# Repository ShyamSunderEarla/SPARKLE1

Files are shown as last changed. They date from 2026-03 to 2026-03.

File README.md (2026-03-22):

This is a multifunctional flight computer which uses an STM32F722 microcontroller for data processing and commands. The sensors used in this are LSM6dS3 as the IMU and MS5611 as the barometer for the altitude measuremet. This has an onboard 5v and 3.3v buck converters. There is an onboard flash for data logging along with an SD card slot.

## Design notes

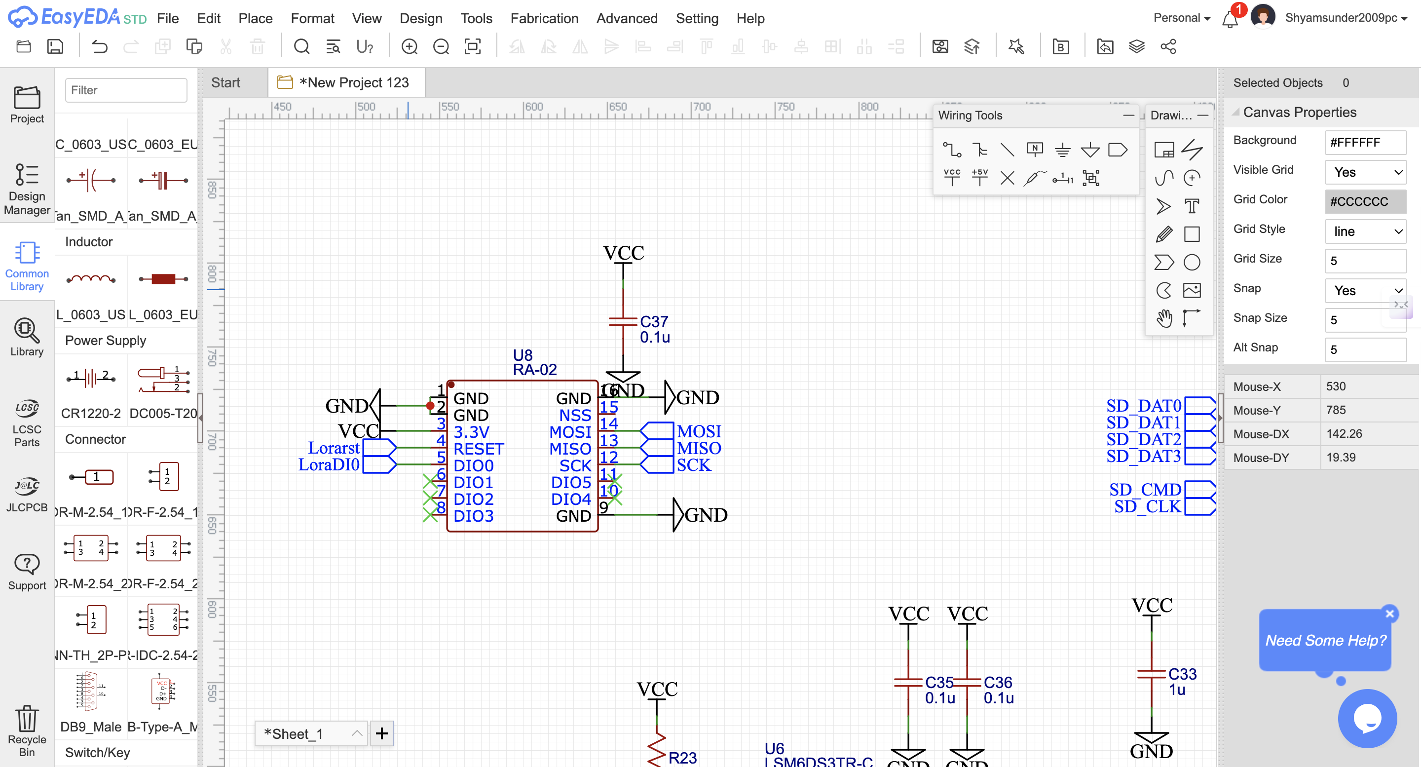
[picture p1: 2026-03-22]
assets/Screenshot 2026-03-17 at 1.37.54 PM.png

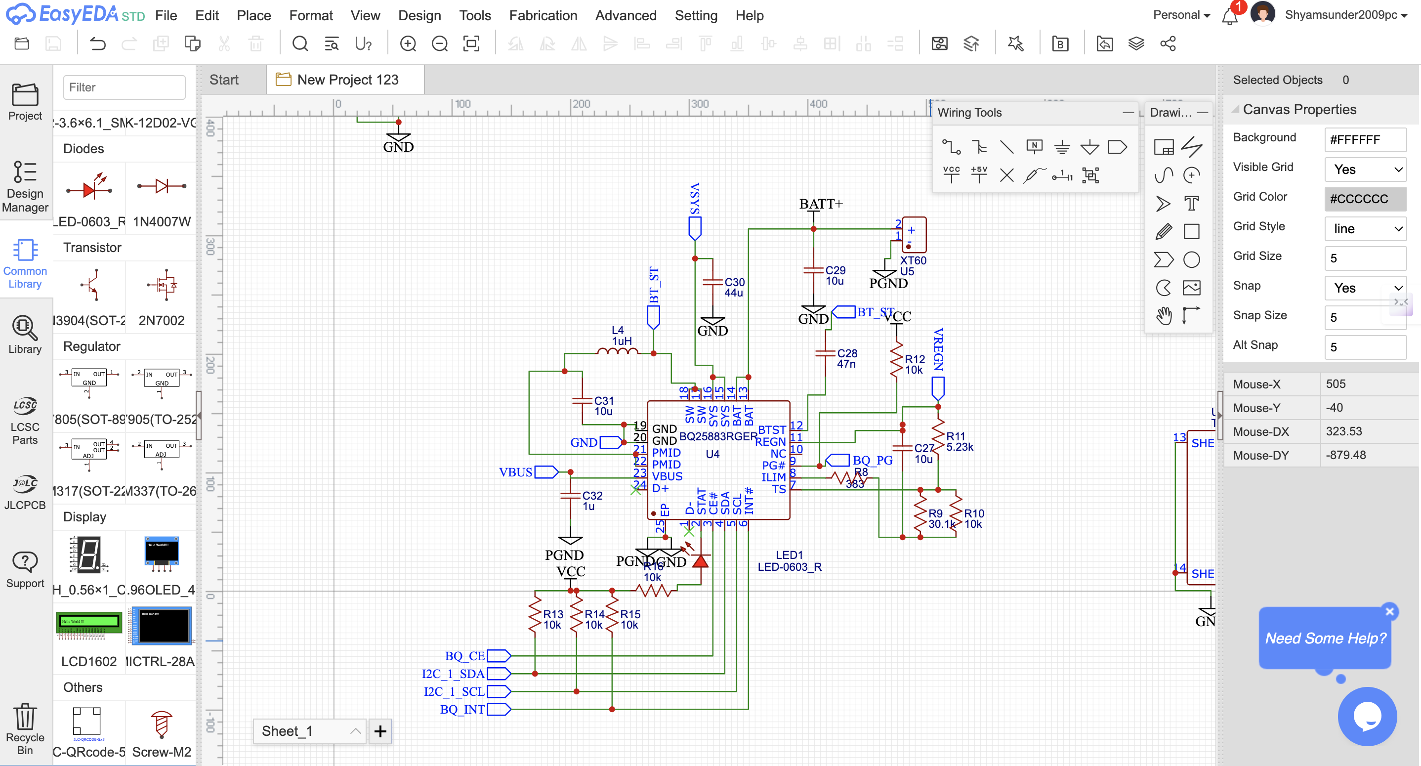
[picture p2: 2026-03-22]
assets/Screenshot 2026-03-16 at 3.34.25 PM.png

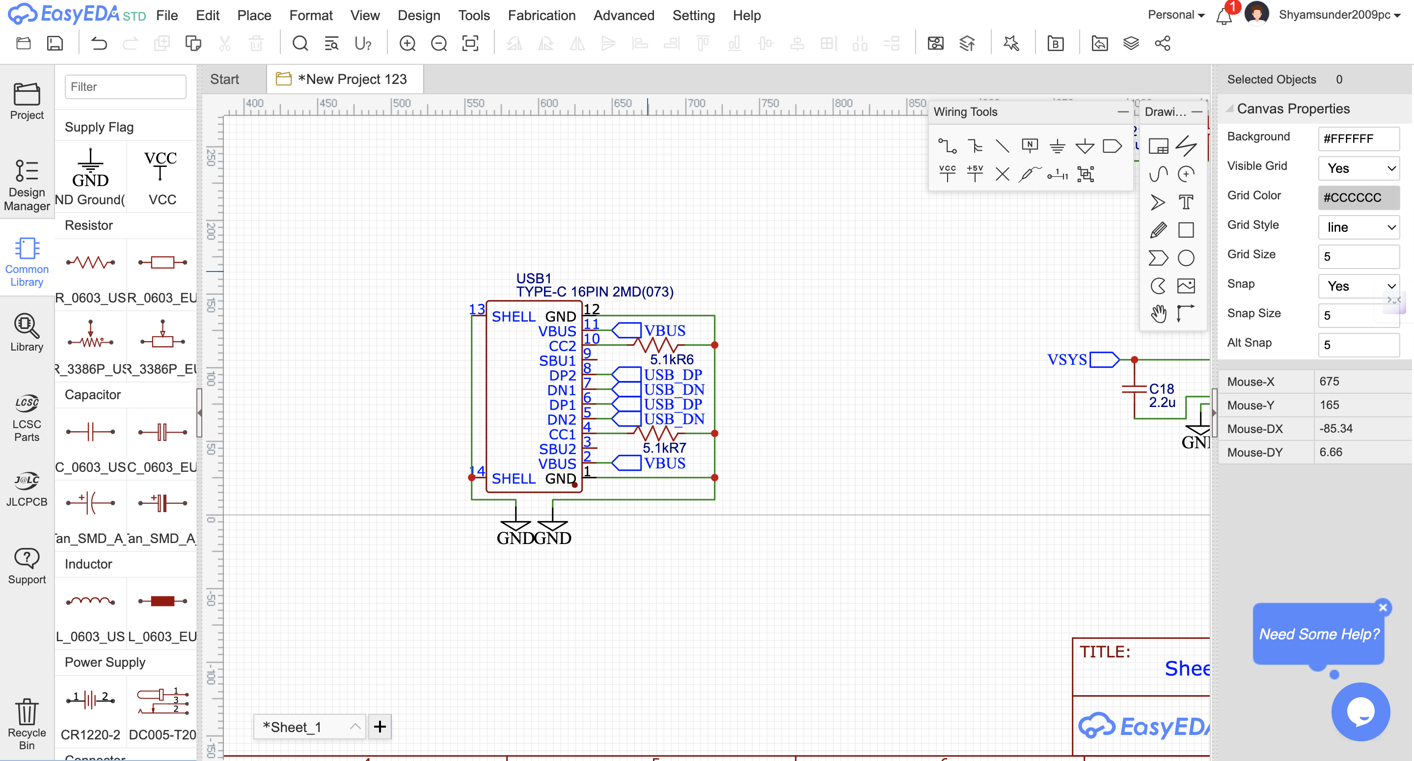
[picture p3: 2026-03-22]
assets/Screenshot 2026-03-16 at 2.43.29 PM.png

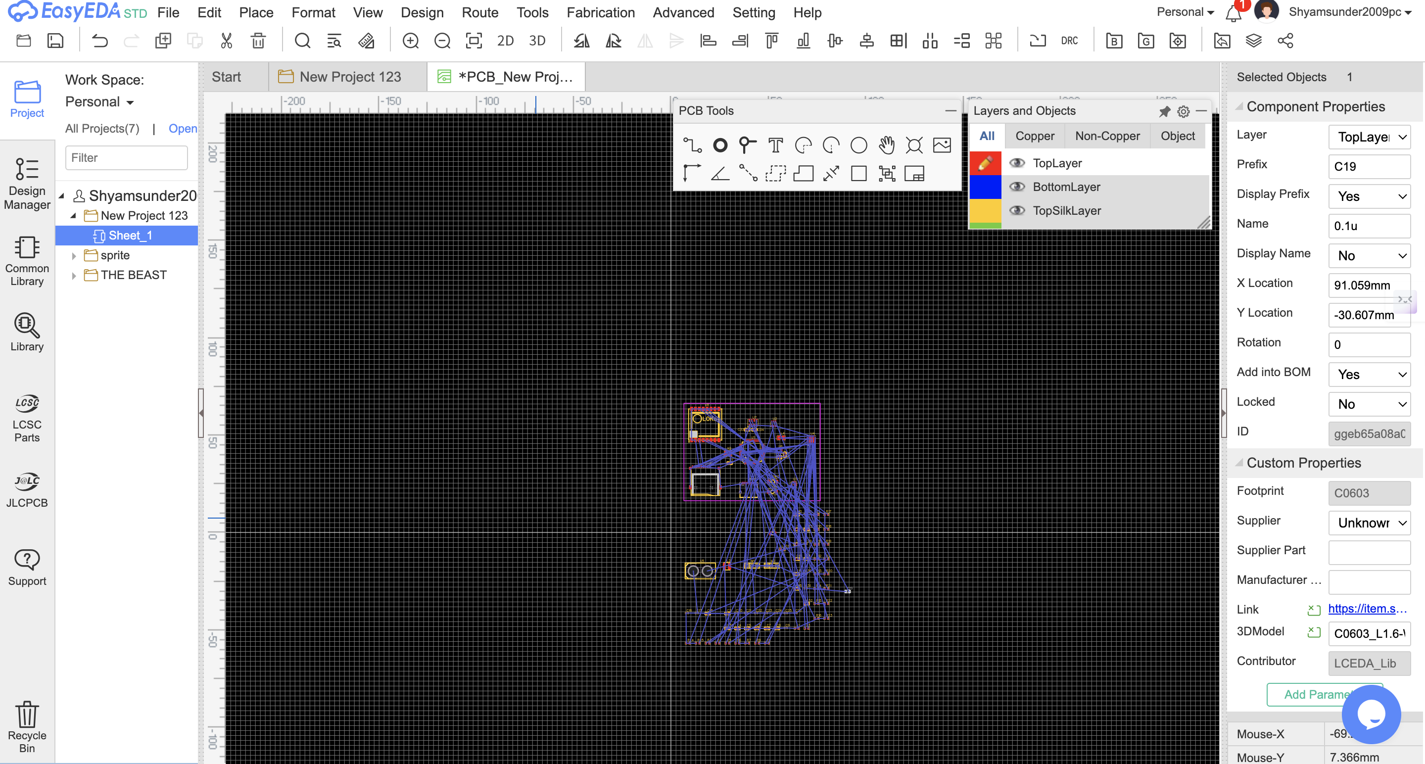
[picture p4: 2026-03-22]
assets/Screenshot 2026-03-18 at 9.15.15 AM.png

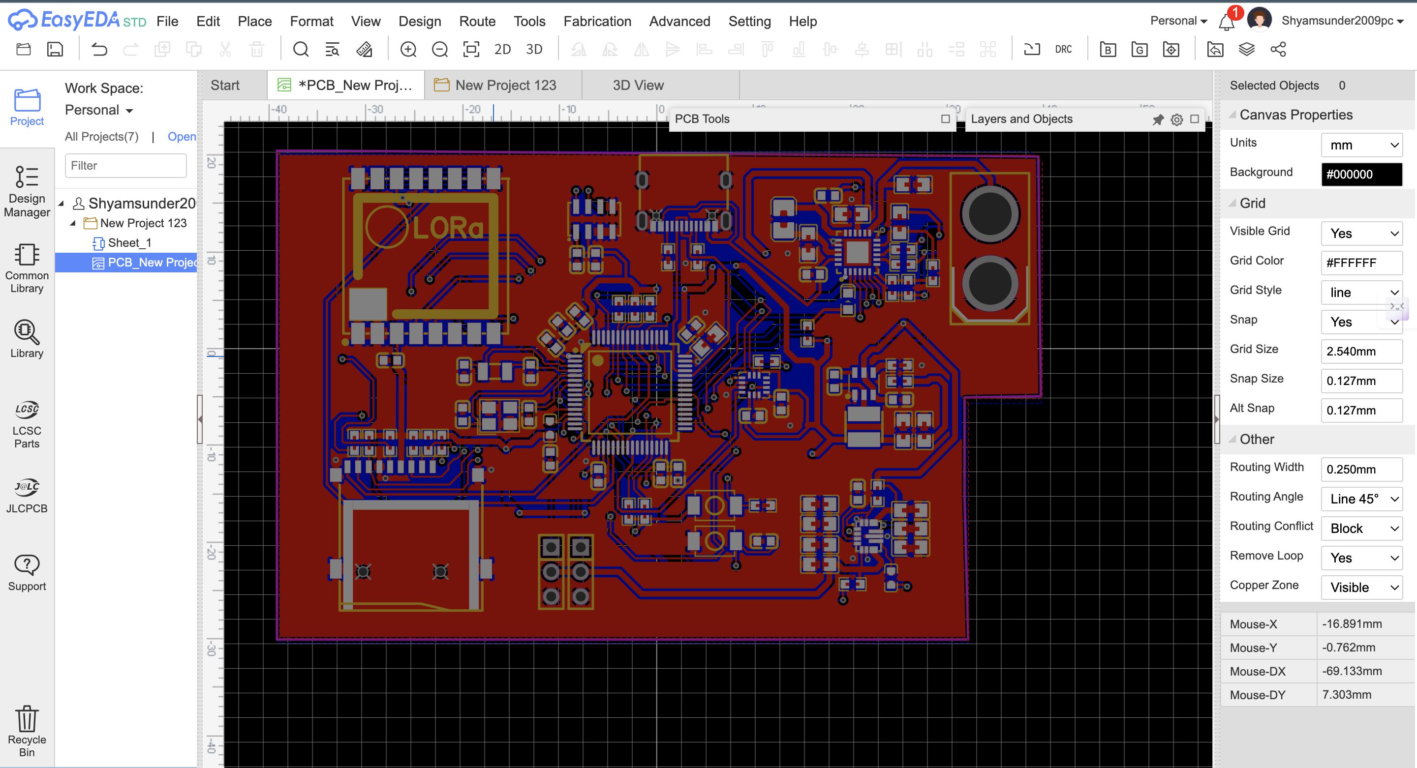
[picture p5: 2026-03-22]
assets/Screenshot 2026-03-22 at 12.50.01 PM.png

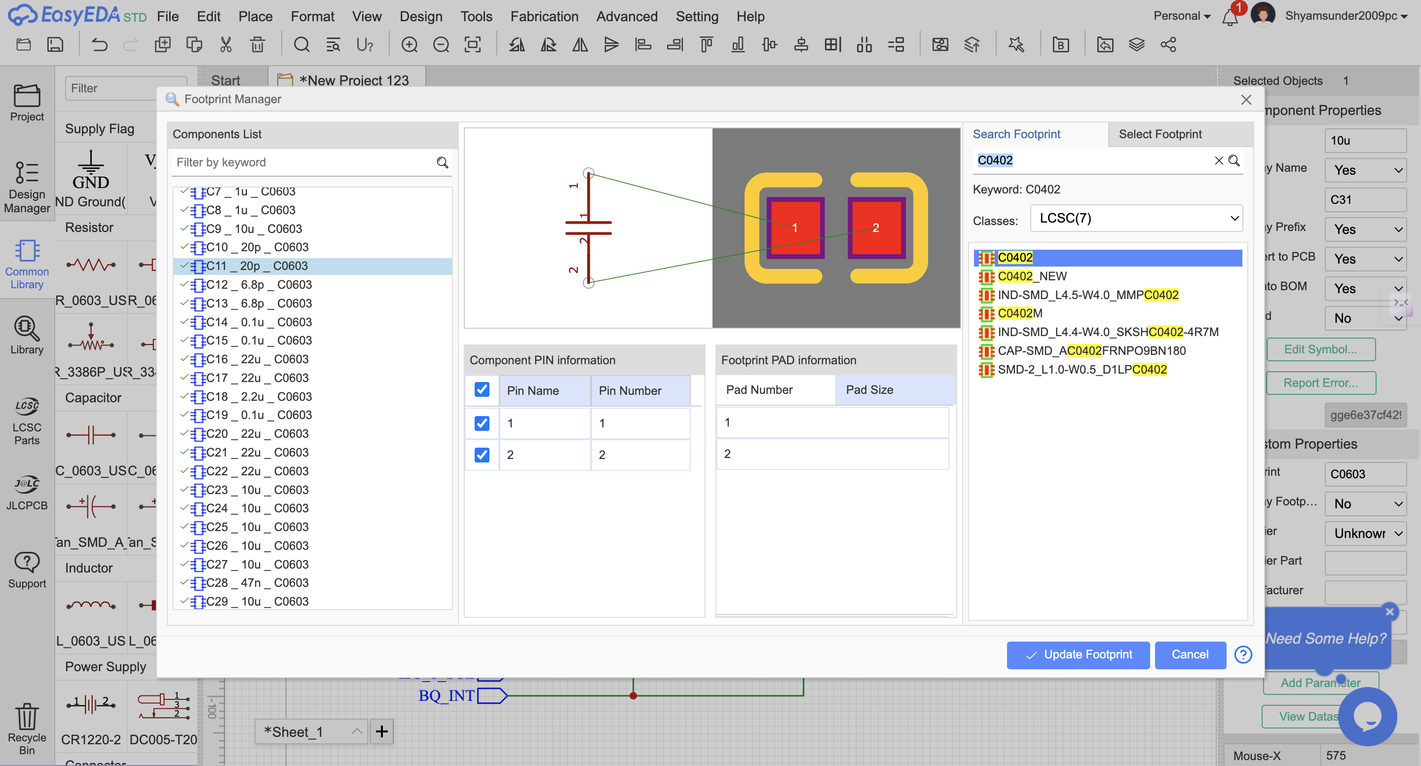
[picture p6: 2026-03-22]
assets/Screenshot 2026-03-17 at 1.45.49 PM.png

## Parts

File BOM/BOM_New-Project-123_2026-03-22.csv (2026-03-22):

ID | Name | Designator | Footprint | Quantity | Manufacturer Part | Manufacturer | Supplier | Supplier Part | Price
1 | 0.1u | C1,C2,C3,C4,C5,C14,C15,C19,C34,C35,C36,C37 | C0603 | 12
2 | 1u | C6,C7,C8,C32,C33 | C0603 | 5
3 | 20p | C10,C11 | C0603 | 2
4 | 6.8p | C12,C13 | C0603 | 2
5 | 2.2u | C18 | C0603 | 1
6 | 47n | C28 | C0603 | 1
7 | TF-01A | CARD1 | TF-SMD_TF-01A | 1 | TF-01A | 韩国韩荣 | LCSC | C91145 | 0.188
8 | FCM1608KF-601T03 | L1 | L0603 | 1 | FCM1608KF-601T03 | TAI-TECH(台庆) | LCSC | C141723 | 0.008
9 | 5.6uH | L2 | IND-SMD_L3.0-W3.0 | 1 | YHNR3015-5R6M | YJYCOIN(益嘉源) | LCSC | C18236327 | 0.009
10 | 1u | L3 | L0603 | 1
11 | 1uH | L4 | L2520 | 1 | DFE252012F-1R0M=P2 | muRata(村田) | LCSC | C435392 | 0.14
12 | LED-0603_R | LED1 | LED0603_RED | 1 | 19-217/R6C-AL1M2VY/3T | EVERLIGHT(台湾亿光) | LCSC | C72044 | 0.021
13 | Motor_Servo | M1,M2 | HDR-TH_PZ254V-11-03P-YL | 2
14 | 10k | R1,R4,R5,R10,R12,R13,R14,R15,R16,R17,R18,R19,R20,R21,R22,R23 | R0603 | 16
15 | 100k | R2 | R0603 | 1
16 | 22.1k | R3 | R0603 | 1
17 | 5.1k | R6,R7 | R0603 | 2
18 | 383 | R8 | R0603 | 1
19 | 30.1k | R9 | R0603 | 1
20 | 5.23k | R11 | R0603 | 1
21 | 2k2 | R24,R25 | R0603 | 2
22 | TS-1088-AR02016 | SW1,SW2 | SW-SMD_L3.9-W3.0-P4.45 | 2 | TS-1088-AR02016 | XUNPU(讯普) | LCSC | C720477 | 0.054
23 | STM32F722RET6 | U1 | LQFP-64_L10.0-W10.0-P0.50-LS12.0-BL | 1 | STM32F722RET6 | ST(意法半导体) | LCSC | C118207 | 6.353
24 | LMR51430XDDCR | U2 | SOT-23-6_L2.9-W1.6-P0.95-LS2.8-BL | 1 | LMR51430XDDCR | TI(德州仪器) | LCSC | C5185863 | 0.913
25 | BQ25883RGER | U4 | VFQFPN-24_L4.0-W4.0-P0.50-BL-EP2.8 | 1 | BQ25883RGER | TI(德州仪器) | LCSC | C544362 | 2.977
26 | XT60 | U5 | CONN-TH_XT60 | 1 | XT60-M. | AMASS(艾迈斯) | LCSC | C98733 | 0.322
27 | LSM6DS3TR-C | U6 | LGA-14_L3.0-W2.5-P0.50-TL | 1 | LSM6DS3TR-C | ST(意法半导体) | LCSC | C967633 | 2.789
28 | MS561101BA03-50 | U7 | SENSORS-SMD_MS5611-01BA03 | 1 | MS561101BA03-50 | TE Connectivity(泰科电子) | LCSC | C15639 | 6.615
29 | RA-02 | U8 | WIRELM-SMD_RA-02-BL | 1 | Ra-02 | Ai-Thinker(安信可) | LCSC | C90039 | 7.011
30 | TYPE-C 16PIN 2MD(073) | USB1 | USB-C-SMD_TYPE-C-6PIN-2MD-073 | 1 | TYPE-C 16PIN 2MD(073) | SHOU HAN(首韩) | LCSC | C2765186 | 0.065
31 | 32.768kHz | X1 | FC-135R_L3.2-W1.5 | 1 | Q13FC13500004 | EPSON(爱普生) | LCSC | C32346 | 0.176
32 | 25MHz | X2 | CRYSTAL-SMD_4P-L3.2-W2.5-BL | 1 | X322525MOB4SI | YXC(扬兴晶振) | LCSC | C9006 | 0.073
33 | 10u | C9,C23,C24,C25,C26,C27,C29,C31 | C0805 | 8
34 | 22u | C16,C17,C20,C21,C22 | C0805 | 5
35 | 44u | C30 | C0805 | 1
36 | TPS63070RNMR | U3 | VQFN-15-HR(3X2.5) | 1 | TPS63070RNMR | TI(德州仪器) | LCSC | C109322 | 1.38

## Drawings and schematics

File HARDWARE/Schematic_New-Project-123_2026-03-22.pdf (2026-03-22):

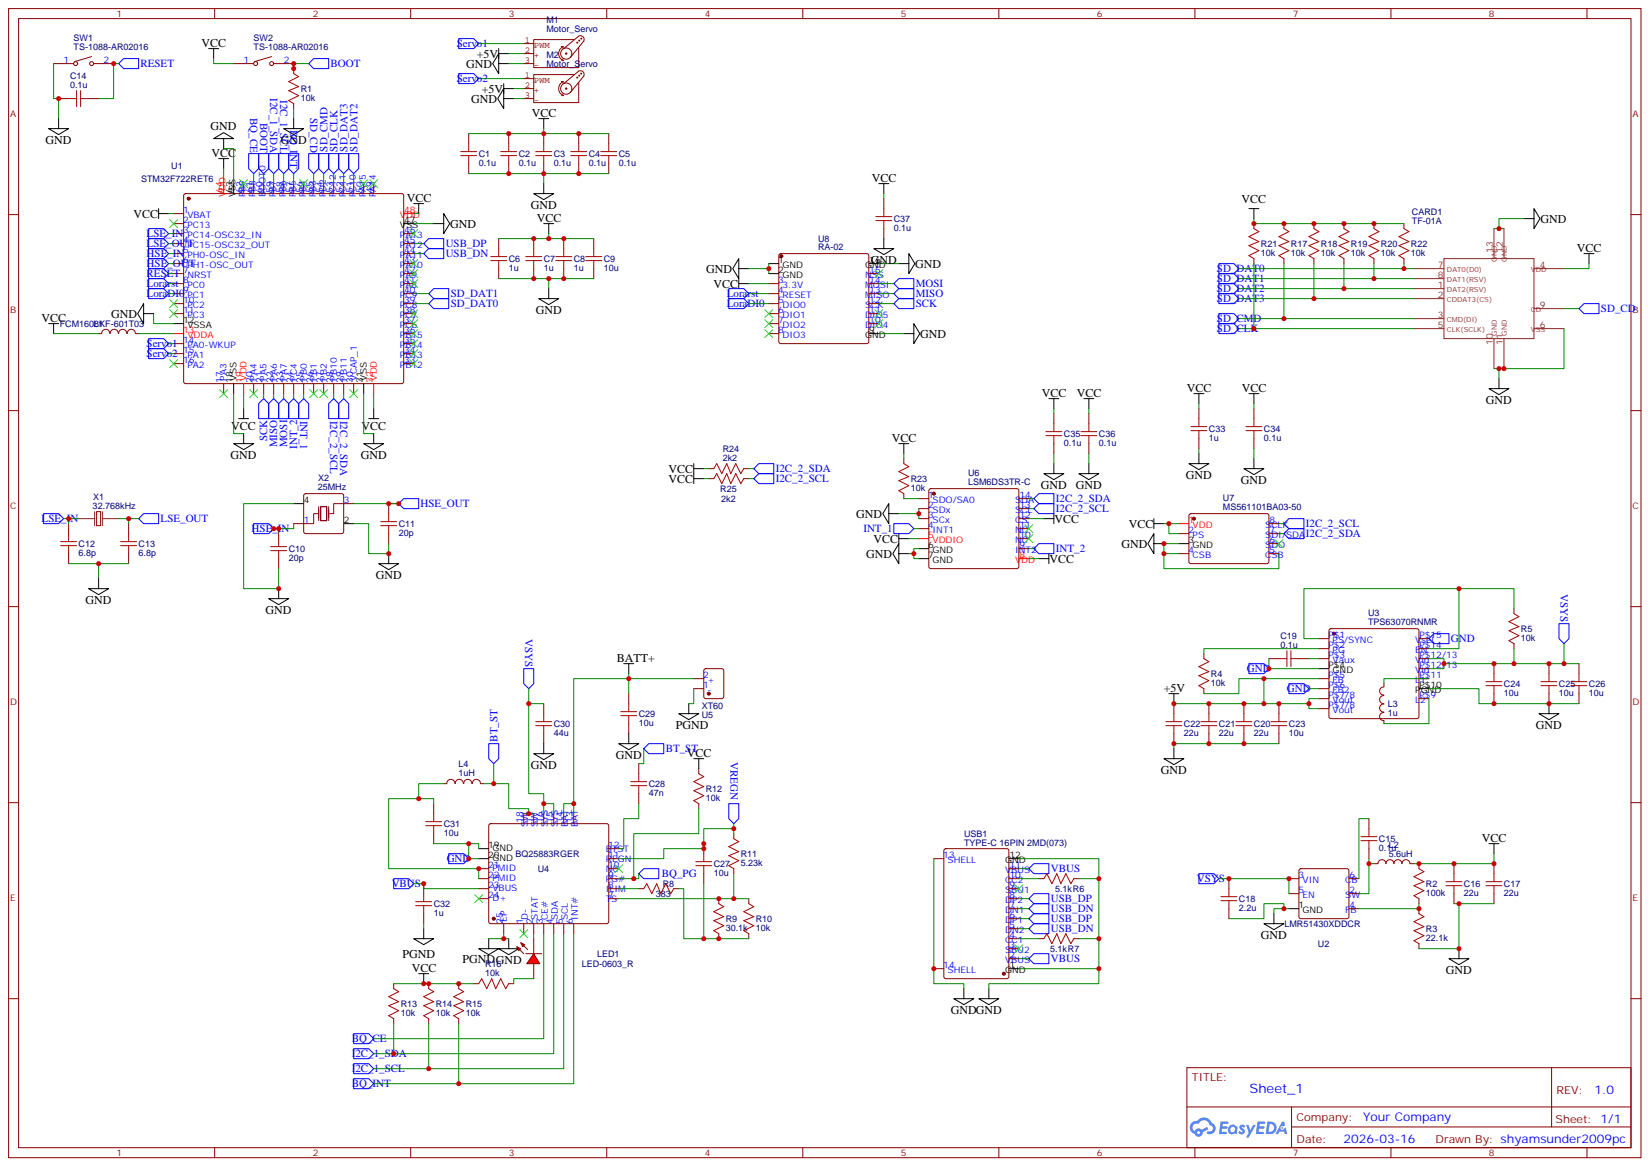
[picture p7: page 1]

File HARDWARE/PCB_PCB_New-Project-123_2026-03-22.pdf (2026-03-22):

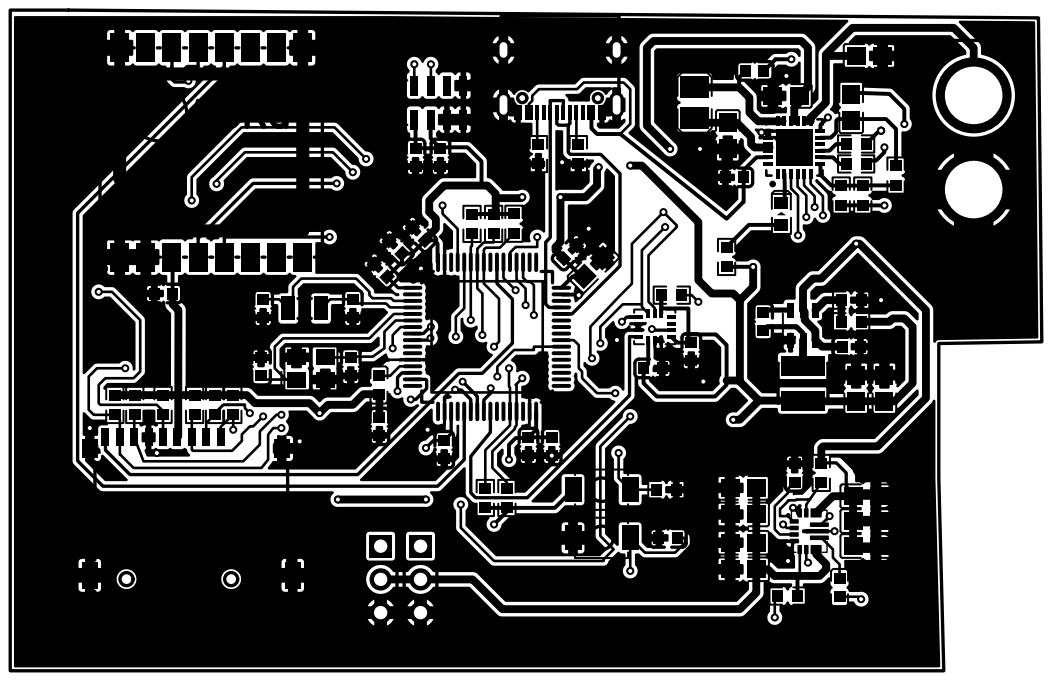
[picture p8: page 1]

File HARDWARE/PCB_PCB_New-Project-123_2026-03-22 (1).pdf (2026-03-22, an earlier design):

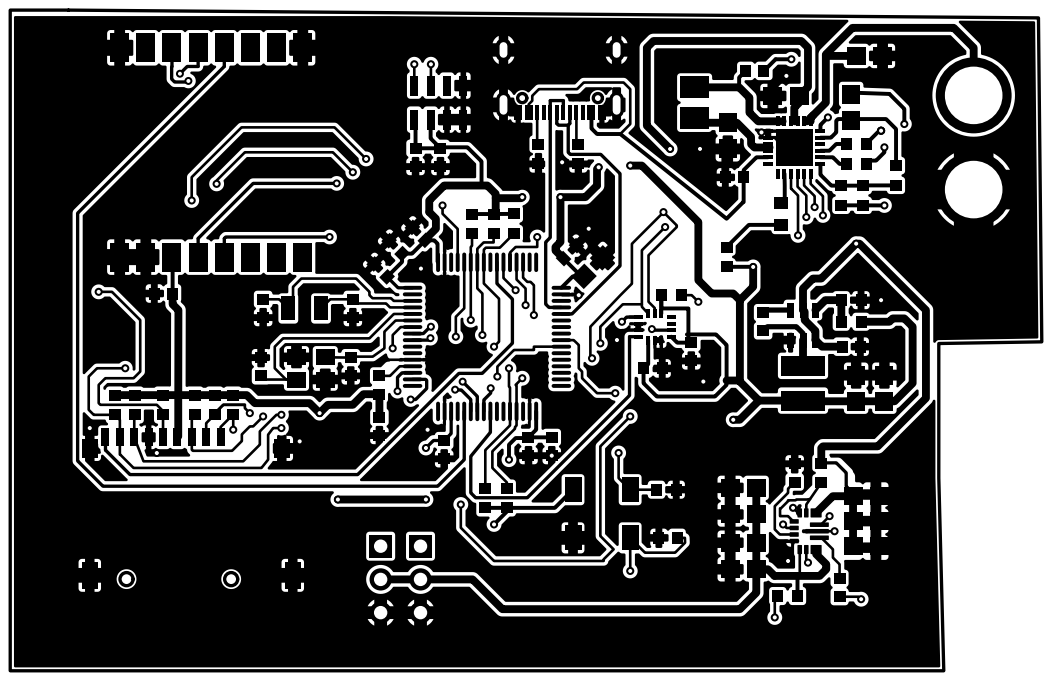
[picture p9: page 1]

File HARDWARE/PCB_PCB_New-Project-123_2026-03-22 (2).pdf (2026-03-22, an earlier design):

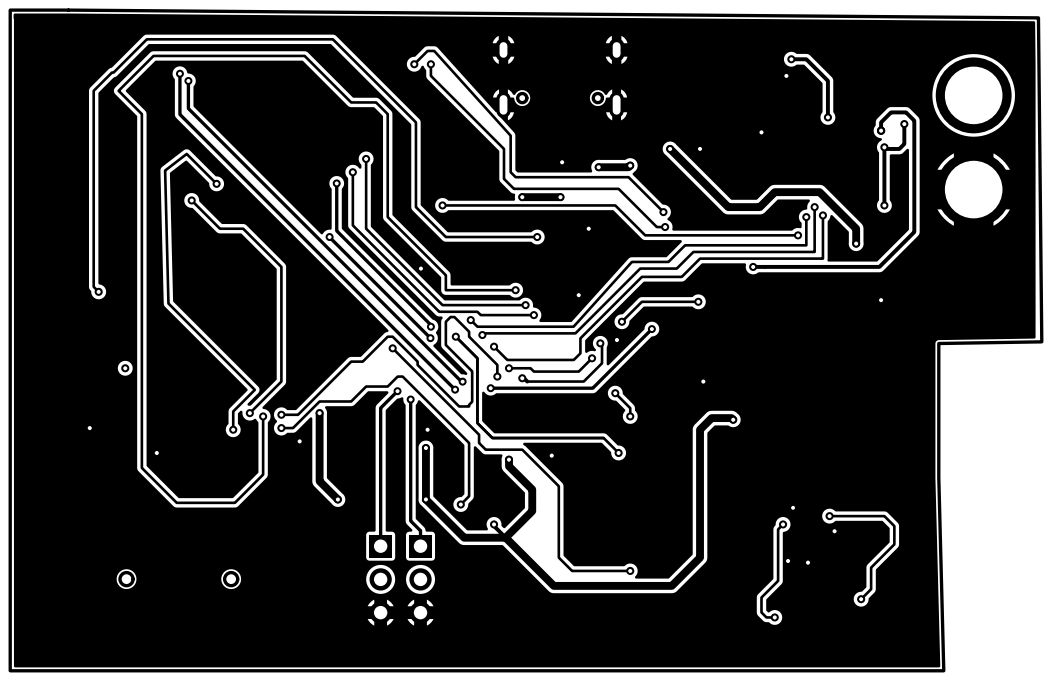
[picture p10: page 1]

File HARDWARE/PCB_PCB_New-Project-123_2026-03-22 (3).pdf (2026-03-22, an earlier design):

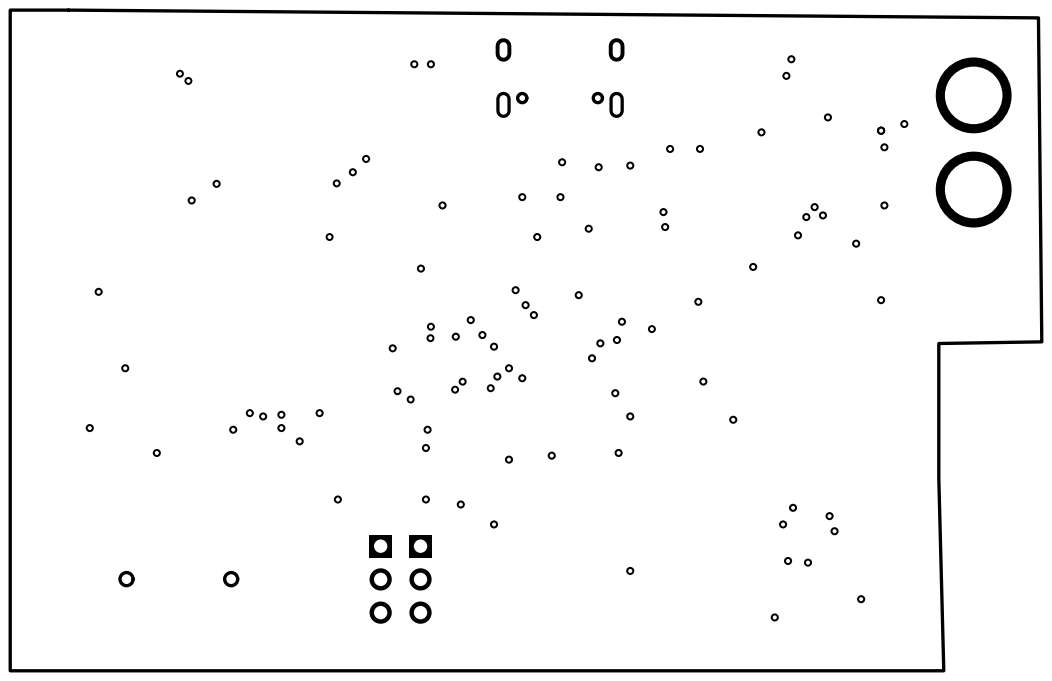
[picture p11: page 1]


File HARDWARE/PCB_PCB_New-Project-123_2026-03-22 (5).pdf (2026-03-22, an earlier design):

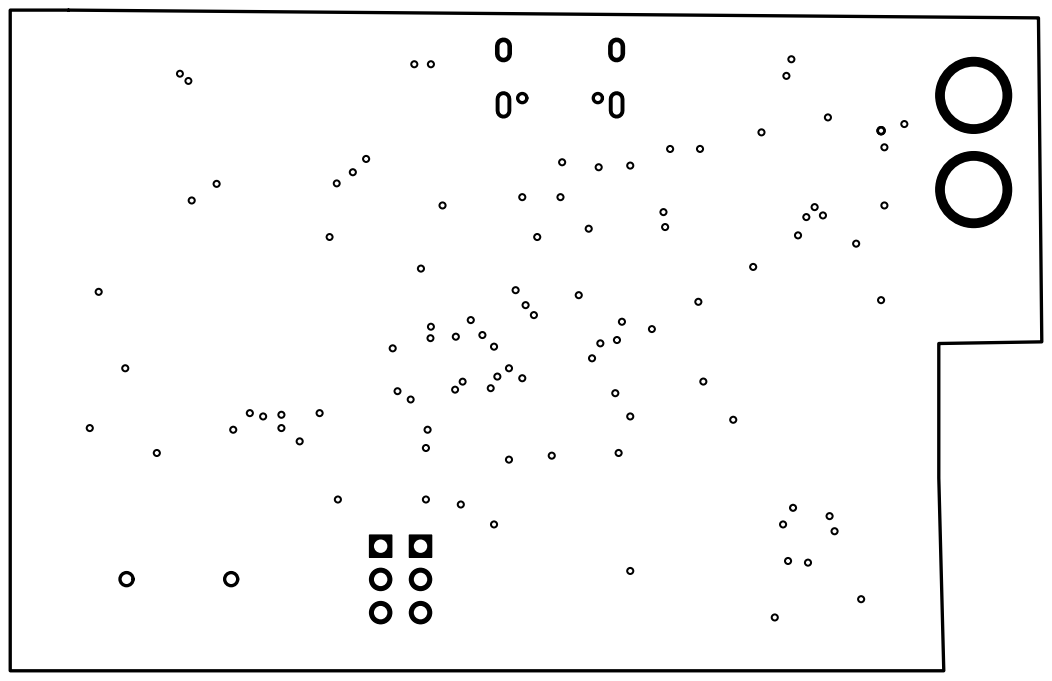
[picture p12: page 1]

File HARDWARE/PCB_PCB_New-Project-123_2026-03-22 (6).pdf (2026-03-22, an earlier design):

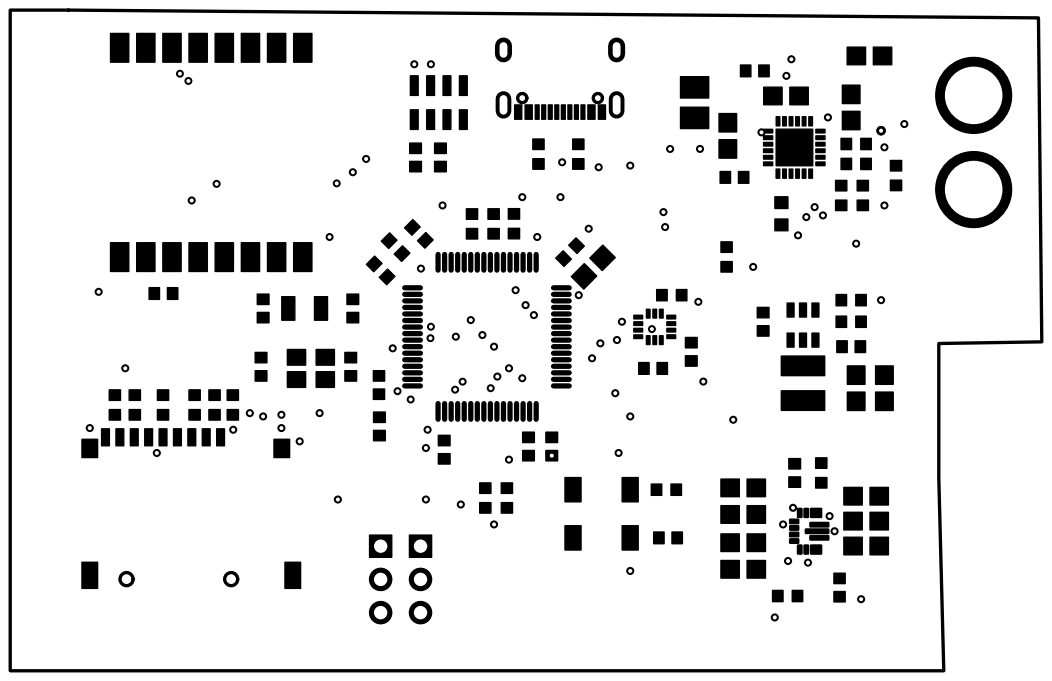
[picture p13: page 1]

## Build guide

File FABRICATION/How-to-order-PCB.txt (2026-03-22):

How to Order PCB

Please refer to:
https://docs.easyeda.com/en/PCB/Order-PCB

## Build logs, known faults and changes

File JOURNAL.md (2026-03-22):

<!--
  This journal is auto generated by Stasis.
-->

# 3/22/2026 7 AM - Routing

_Time spent: 4.5h_

I did routing today. I made sure the traces of 3.3v and 5v were at least 0.3mm, and the main trace was 0.6 mm. It took a lot of time while routing the tps63070  due to an improper footprint, but somehow I finally achieved it. The traces from the SD card to the MCU became too long. I added ground power planes on both layers (the top and bottom copper layers). I wanted to make a 4-layer PCB, but to make the PCB a bit cheaper, I did a 2-layer PCB. I kept the rest of the traces 0.2mm. But the traces from decoupling capacitors were 0.3mm. I took a lot of time, so I did 2 hours the previous day and another 2.5 hours this day. Although the routing of the 2-layer PCB was tough for some of the SPI lines, I used the autorouter in EASYEDA. I faced a lot of problems at the end of PCB while doing DRC. At first, it showed so many errors, but later I managed to correct all the errors I made while routing.










# 3/21/2026 7 AM - pcb

_Time spent: 2.5h_

I placed the components by following all the design rules, then suddenly changed the footprints of some of the components( capacitors of values 10u to 44u). I tried to possibly keep the imu at the centre of the PCB to get error-free values, and placed the barometer near the edge of the PCB. I kept the power section (buck converter, battery charger on one side of the PCB. I faced some challenges while placing the decouplers. I placed each one by measuring its distance from the pad on the component.










# 3/17/2026 8 AM - stm32 schematic

_Time spent: 2h_

I did the decouplers for MCU, the boot and reset switches, the main schematic, the oscillators, etc.













# 3/17/2026 8 AM - stm32

_Time spent: 1h_

I started with stm32cubemx i configured the pinout according to my need.










# 3/17/2026 8 AM - sensors

_Time spent: 0.5h_

I completed the sensors schematic and the lora schematic. I added decouplers and etc. to reduce noise. 










# 3/16/2026 10 AM - Powering the pcb

_Time spent: 2h_

I worked on the battery charger, SD card, and usb c pin. I went through the tutorial of @NotaRoomba (blueprint starter projects) for guidance. I got confused a lot while working on the battery charger, but I could manage well. The SD card and C pin were like easy stuff, but reading the battery charger datasheet is absolutely recommended. and thats it for now.










# 3/16/2026 6 AM - Schematic

_Time spent: 2h_

Started with schematic added components to schematic , gave power supply connections and added bucks, sensors and etc. Its been a cold start of wiring the 5v buck regulator but managed to do it.










# 3/16/2026 5 AM - Component selection

_Time spent: 2h_

I searched for components I followed @NotARoomba (from blueprint) I've chosen STM32F722 as the main processing unit. I chose the sensors LSM6DS3 and MS5611.










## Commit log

2026-03-22 Create PCB
2026-03-22 Create PCB files
2026-03-22 Create Bom
